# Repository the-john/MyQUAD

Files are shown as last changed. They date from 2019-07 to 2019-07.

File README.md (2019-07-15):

# MyQUAD
First Open Source Arduino Based Quad Copter

Back in the day, gaining access to a Quad Copter wasn't easy.  Especially one that you could intimately know and modify.  I set out to change that.

I wanted to develop a platform that "students" could come to know and understand.  My hope was to inspire students from all walks of life to learn and grow.  I hope I did that with the material in this repository.  After I developed this material, I handed it over to others who promised to make it all publically available.  I'm not convenced that they did a very good job of that.  So, I've placed the materials here in this repository for public consumption.  (Albeit, SEVEN YEARS LATER!)

At the time, I chose to develop the Quad Copter on an Arduino board.  I had already gotten many people, mostly students, excited about the Arduino board with Introductory Training materials that I had created on my own previously.  I knew that the Arduino platform would be easy for NOOBs to wrap thier brain around and get them hooked.  So I designed a Quad Copter Shield and set off to develop a complete kit.  I purposely designed the Shield in Eagle to enable others to modify or embellish via a free tool.

I looked around for a long time to try and find some code that would work on my new platform.  Though there were code options to be had, most of them required a PhD in Computer Programming to debug if you changed the slightest thing.  I knew this would be a buz kill for my following ... so I personally wrote all of the code from scratch in the Programming language.  This code is also included in the attached material, and I hope you find use in opening it up and playing around with it.

The course is meant to be a week long course; four days of lecture and building, one final day for debugging, code upgrading, and a fly-off contest.  So in a week you should be able to go from total NOOB to a flying platform, over 1500 other students have done so themselves.

Good luck, and have some fun with this!

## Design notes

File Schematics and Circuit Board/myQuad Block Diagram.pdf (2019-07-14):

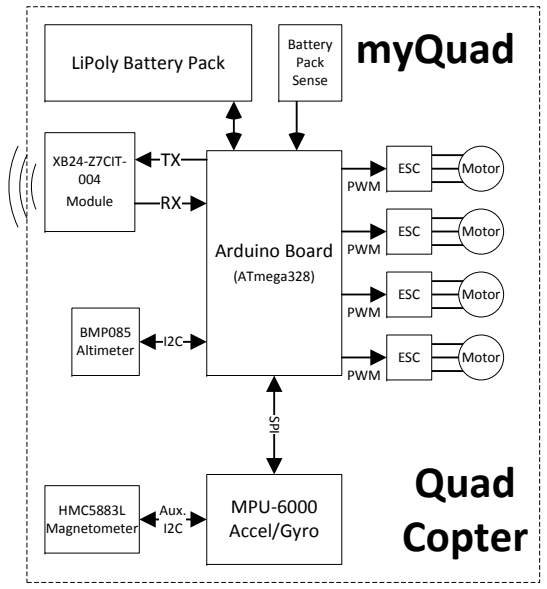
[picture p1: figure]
XB24-Z7CIT- 004 Module; Arduino Board; (ATmega328); Quad Copter; ESC; Motor; PWM; MPU-6000 Accel/Gyro; SPI; LiPoly Battery Pack; Battery Pack Sense; Aux. I2C; BMP085 Altimeter; HMC5883L Magnetometer; myQuad

# Laptop Computer

USB Dongle

## ZigBee Wireless

XB24-Z7CIT-004
Module

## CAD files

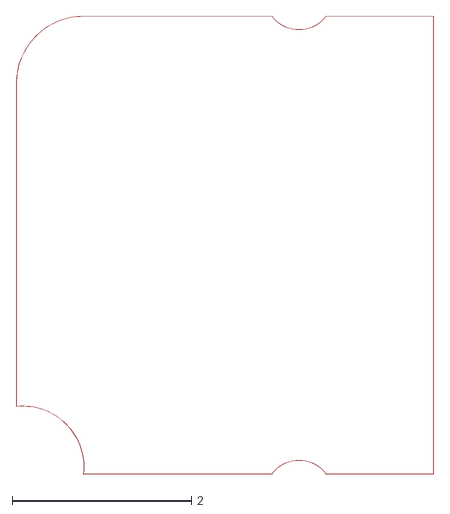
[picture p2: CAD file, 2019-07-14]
Schematics and Circuit Board/Shield Design/Examples/outline.dxf
4.66 x 5.11

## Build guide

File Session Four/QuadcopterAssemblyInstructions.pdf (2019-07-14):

Intel Ultimate Engineering Experience (IUEE)

Chandler Embedded Innovation Center (CEIC)

## IUEE

Quadcopter Assembly
Quadcopter Assembly – IUEE arms and rotors.
You will need the four plastic cutouts for the “landing gear”. One is blue and is the “front” rotor arm. The other 3 are clear plastic. For each rotor, use 2 shiny metal screws from package #1 (8 total), a gold rotor, a blue arm and a plastic landing gear cutout. Repeat for each rotor/arm assembly.
Place the gold rotor on top of a blue arm. Using a Phillips screwdriver, connect the plastic landing gear cutout below the arm with the 2 screws. The screws should connect the plastic landing gear, the arm and the rotor together. The rotor wires should be on the same side (left, when looking toward the center of the copter) of the arm assembly.

[HINT: This might take two team members to hold the components in place.

A shortcut -Try screwing one screw with just the rotor and arm, to align the holes, on the side without the wires. Then screw in the second screw through the plastic landing gear, the arm and the rotor, tightly. Now, remove the first screw (be careful when removing the screw, it may ‘pop’ out at you!), push the plastic landing gear in place and tighten. ] You should now have 4 rotor arm assemblies ready for the next step.
Quadcopter Assembly – rotor arm to center base.
You will need the four rotor arm assemblies, the “odd” shaped center plastic base, 8 black plastic screws, and 8 dull metal standoffs (size?).

Connect each of the 4 rotor arm assemblies to the base using 2 of the screws and the standoffs (as shown in the model).

[HINT: Notice the base pattern. The narrower edges connect to the front and back rotor arm assemblies. The wider edges connect to the side rotor arm assemblies.]
Quadcopter Assembly – rotor arm to center base.
You will need the four rotor arm assemblies, the “odd” shaped center plastic base, 8 black plastic screws, and 8 dull metal standoffs (size?).

Connect each of the 4 rotor arm assemblies to the base using 2 of the screws and the standoffs (as shown in the model).

[HINT: Notice the base pattern. The narrower edges connect to the front and back rotor arm assemblies. The wider edges connect to the side rotor arm assemblies.]
Quadcopter Assembly – Connect Arduino and shield to base.
You will need the center base assembly (assembled with the rotor arms), the Arduino board, the shield board, 4 long plastic standoffs (package #x), 4 short plastic standoffs, 4 long black screws (with a “hex head”), and 4 regular nuts.

The shield will go on top of the Arduino board, separated by the long plastic standoffs. Below that are the short plastic standoffs between the Arduino board and the center base assembly. The four screws go through this whole “stack” of components, and are tightened in place with the regular nuts.

[HINT: This might take two team members to hold the components in place.

Insert a screw thru the shield board, long plastic standoff, and Arduino board. Push the short standoff on, followed by the center base assembly. Tighten loosely, using the nut..

Repeat on an adjacent screw (tilting the board, can be done a bit if the first screw is “loose”). Follow with the next two screws. Then tighten up all 4 screws/nuts.

### Quadcopter Assembly –actuators to rotos

You will need the center base assembly, 4 sets of Velcro, and 4 mini actuator boards.

Connect each set of 3 actuator wires to the rotor. Place the Velcro strip on the bottom of the center base plastic so that the actuator board “lines up” with the green connector on the Shield. Connect up the voltage pins and signal pins. The connectors are + (red wire) and – (black wire) for the voltage pins. The signal pins (green connector) should have the black wire on the board edge and the white wire toward the board center.

[HINT: BE CAREFUL NOT TO JAM THE WIRES TOGETHER TOO HARD. THE WIRES MIGHT BREAK!]

Spin test.
Do a spin test of your rotors. You will need a battery to connect to the Shield board. The front (blue) and rear rotors should be spinning counter-clockwise. The two side rotors should be spinning clockwise.

If a rotor is spinning the wrong direction. Take two of the rotor wires on that rotor and “flip” the connections. This is a 3-phase rotor and that will change the spin direction.

Continue Assembly.
Quadcopter Assembly –Heat shrink placement.
Quadcopter Assembly –center base w/ boards to top plate.
You will need the center base assembly, 8 black nuts, 8 locking nuts, and 8 very long shiny screws (package #).

Connect the top plate (lining up the Intel logo) to the center plate using the nuts and screws.

[HINT: Screw 2 regular nuts down on each screw. Place the screw in the hole on the center assembly. Tighten the locknut. Repeat for other 3 screws. Place the top plate on the screws and tighten the top locknuts. Then tighten the 8 regular nuts, so that the assembly is stable.]

### Quadcopter Assembly – Connect Bottom plate to assembly

You will need the base assembly, 2 velcro straps, 8 black screws, battery, and a voltage buzzer alarm.

Connect the top plate (lining up the Intel logo) to the center plate using the nuts and screws.

[HINT: Screw 2 regular nuts down on each screw. Place the screw in the hole on the center assembly. Tighten the locknut. Repeat for other 3 screws. Place the top plate on the screws and tighten the top locknuts. Then tighten the 8 regular nuts, so that the assembly is stable.]

Position Capacitor Jumpers To Fly

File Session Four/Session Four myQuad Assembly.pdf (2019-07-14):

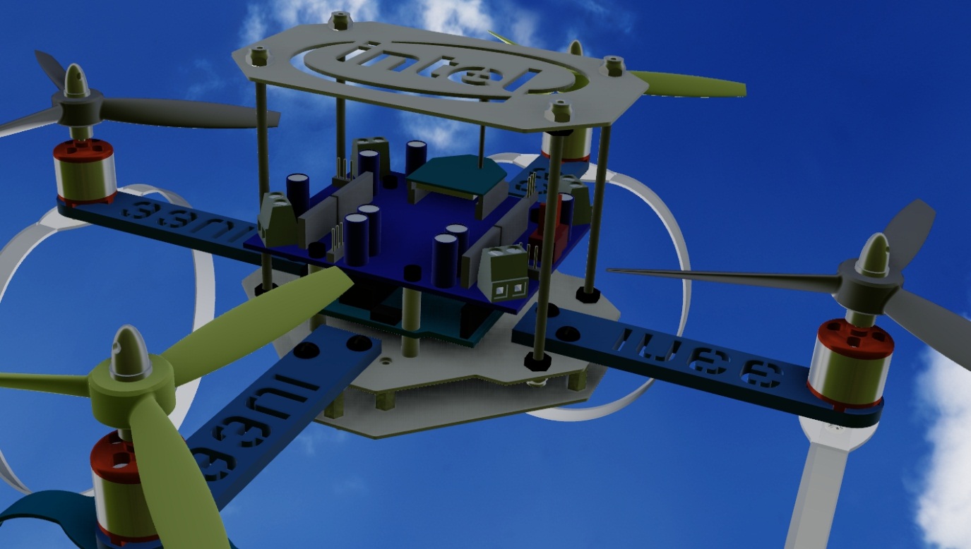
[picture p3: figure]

# Session Four

# Assembly

# Joy Shetler, PhD

# Robotics Week Instructor

# Intel Ultimate Engineering Experience (IUEE)

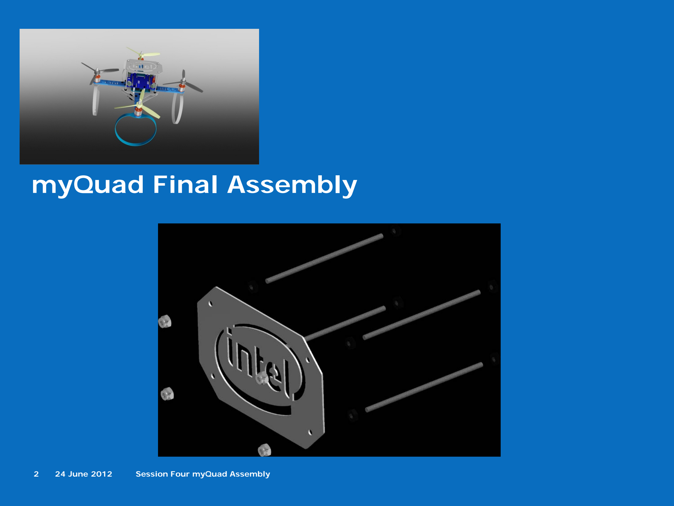
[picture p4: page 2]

2 | 24 June 2012 | Session Four myQuad Assembly

# myQuad Final Assembly

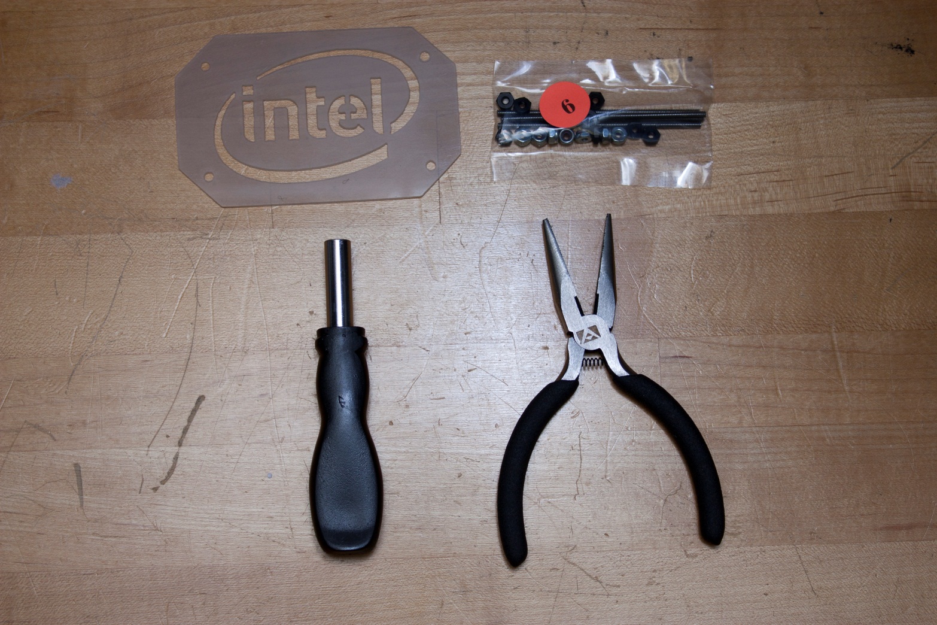
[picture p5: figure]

Chandler Embedded Innovation Center (CEIC)

# Locate Remaining Parts for Crash Protection Plate Mounting

3 24 June, 2012 Session Four myQuad Assembly

# Attach Crash Protection Plate to Mounting Studs

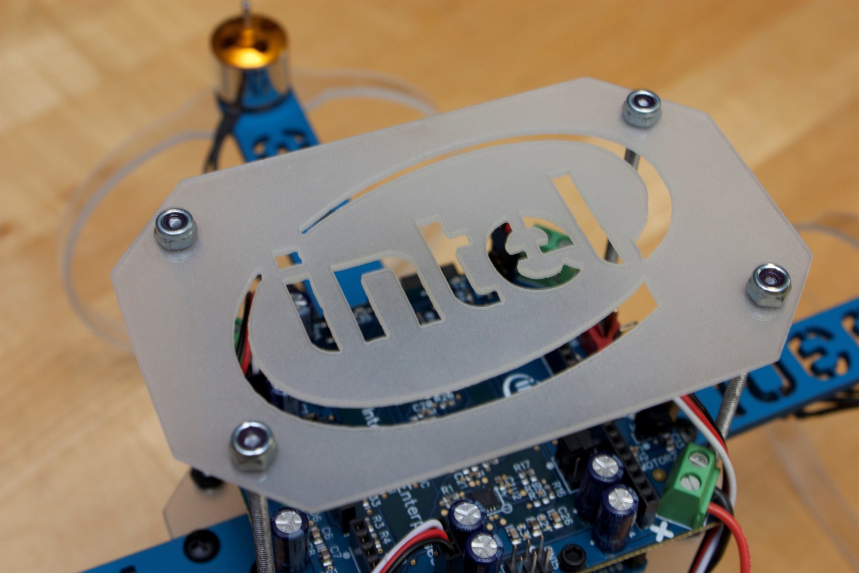
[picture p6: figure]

4 24 June, 2012 Session Four myQuad Assembly

# DANGER

# Do not install propellers until all preliminary testing is

complete.

# Do not run myQuad with propellers outside of

designated safety zone.

5 24 June, 2012 Session Four myQuad Assembly

# Locate Propellers and Propeller Hubs

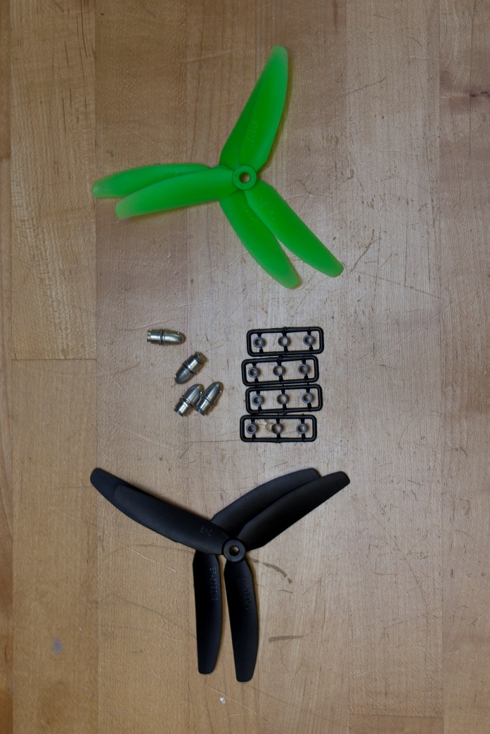
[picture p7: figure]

6 24 June, 2012 Session Four myQuad Assembly

# Attach Propeller Hub Base to Motor Shaft (Insert Plastic Spacer If Applicable)

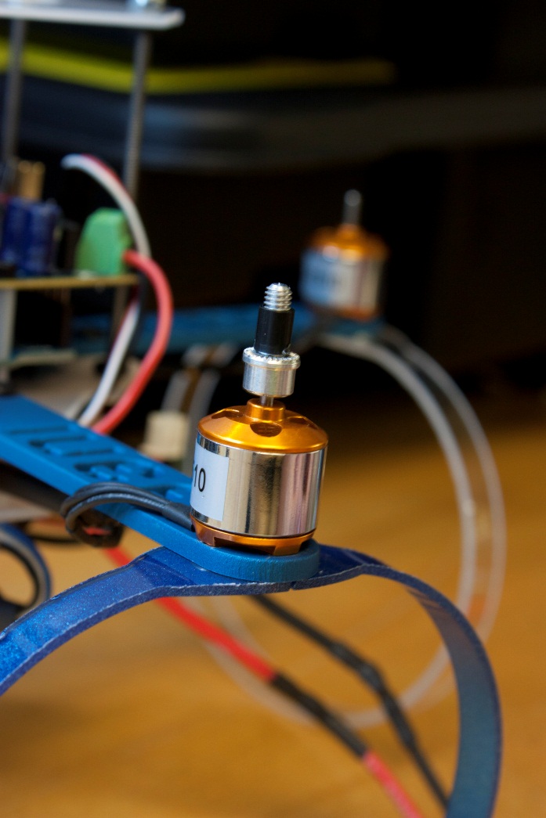
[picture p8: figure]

7 24 June, 2012 Session Four myQuad Assembly

# Slide Propeller Onto Propeller Hub Base

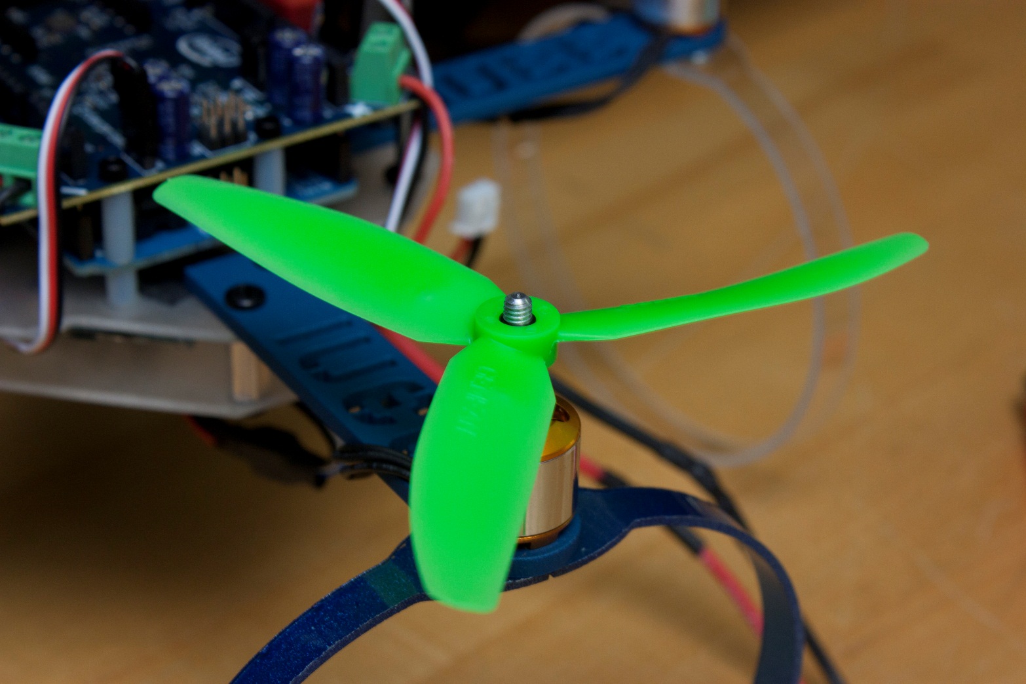
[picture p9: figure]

8 24 June, 2012 Session Four myQuad Assembly

# Attach Propeller Hub Nut, and Tighten

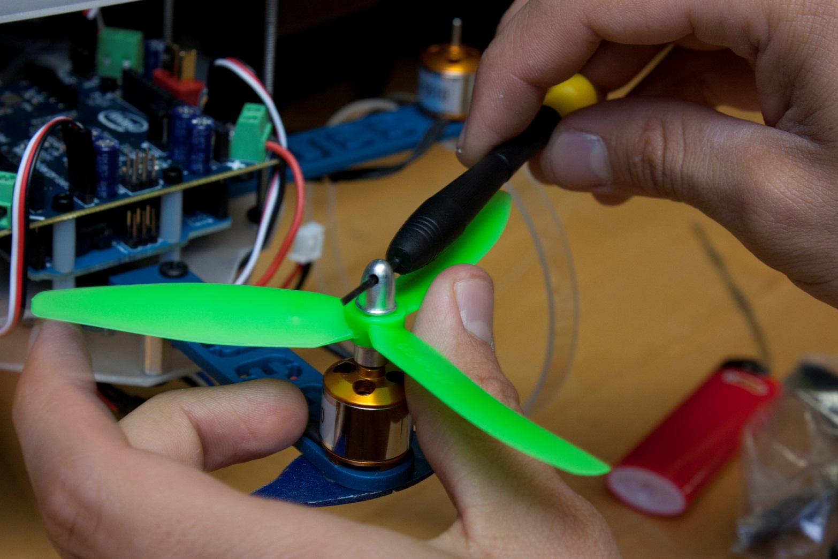
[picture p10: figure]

9 24 June, 2012 Session Four myQuad Assembly

# Front/Back Motors – CW Rotation Props Right/Left Motors – CCW Rotation Props

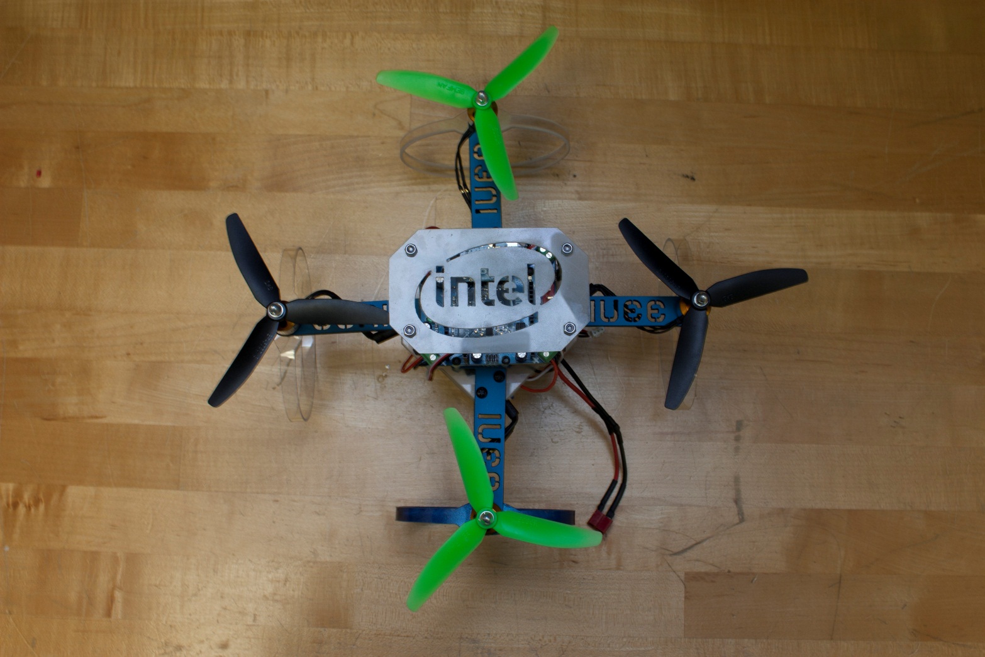
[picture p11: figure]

10 24 June, 2012 Session Four myQuad Assembly

# It’s a beautiful thing…

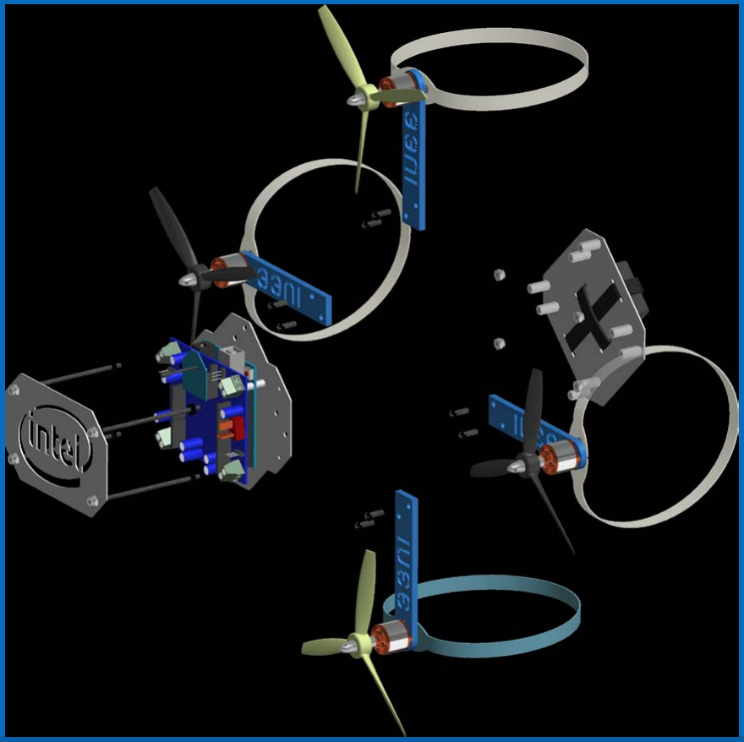
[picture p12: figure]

11 24 June, 2012 Session Four myQuad Assembly

# GO FLY!

12 24 June, 2012 Session Four myQuad Assembly

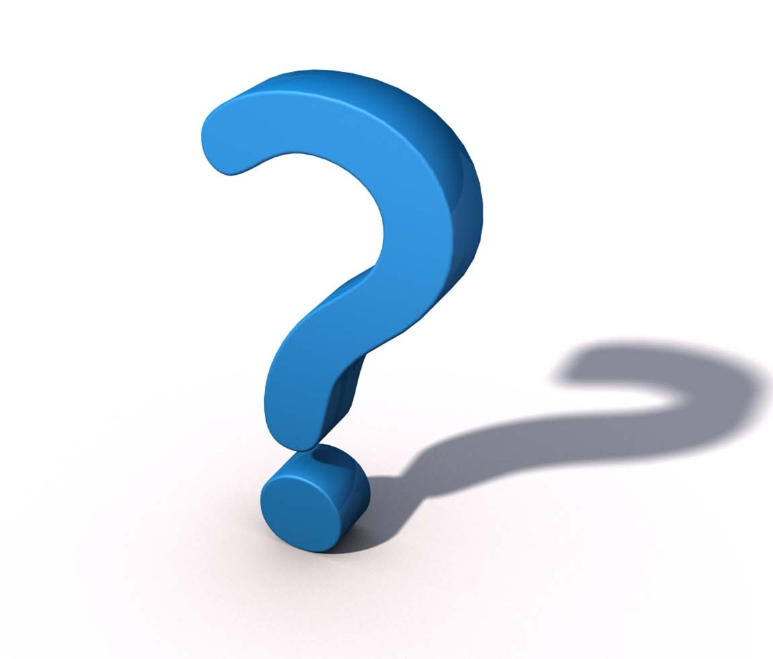
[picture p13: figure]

13 | 24 June, 2012 | Session Four myQuad Assembly

# Questions?

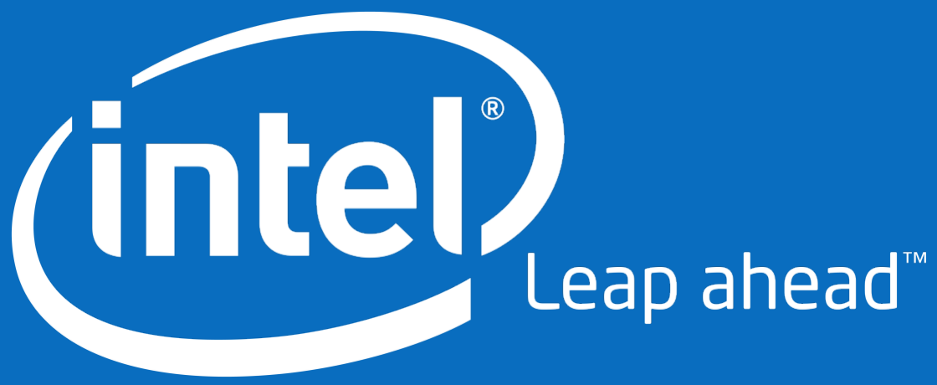
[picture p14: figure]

15 | 24 June, 2012 | Session Four myQuad Assembly

# Backup

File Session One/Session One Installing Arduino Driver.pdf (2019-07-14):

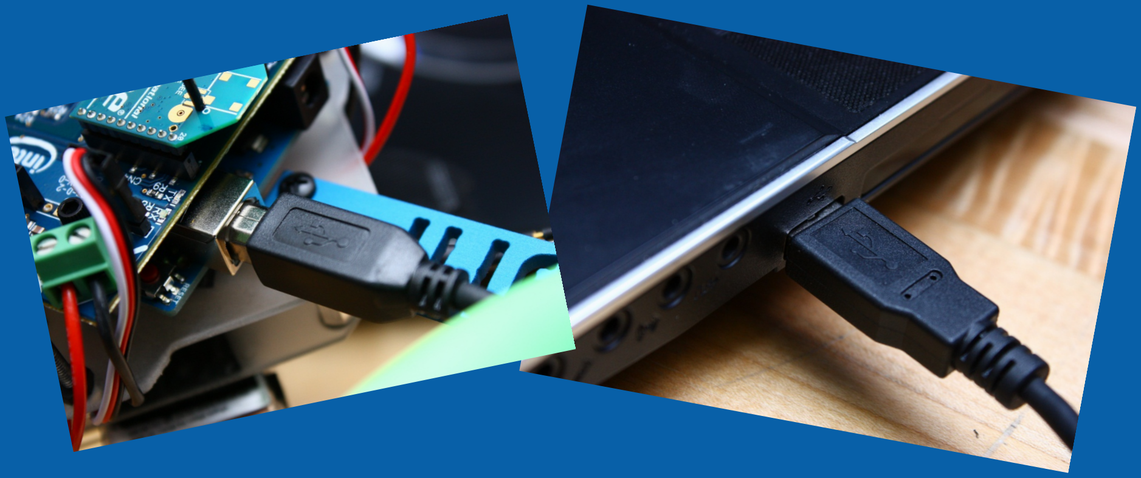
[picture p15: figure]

# Session One

# Installing Arduino Driver

# Joy Shetler, PhD

# Robotics Week Instructor

# Intel Ultimate Engineering Experience (IUEE)

# Connect your Arduino to the Computer

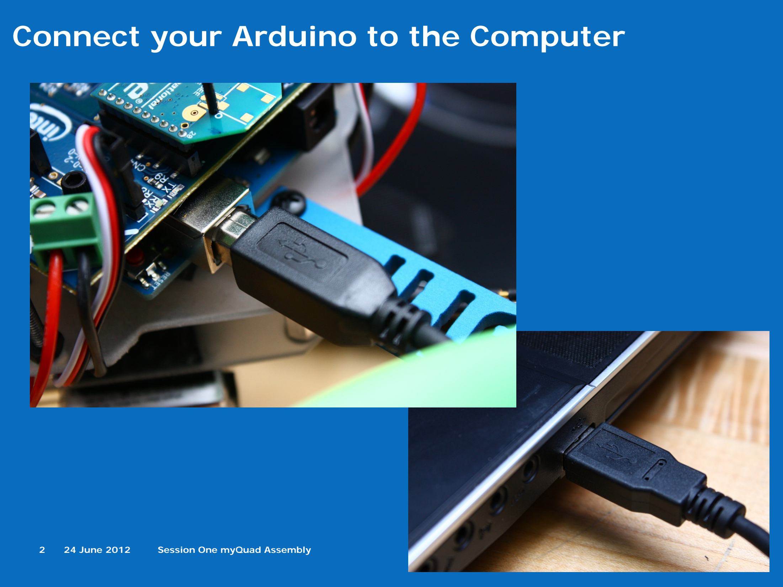
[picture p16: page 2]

2 | 24 June 2012 | Session One myQuad Assembly

# Window Wont Install Drivers

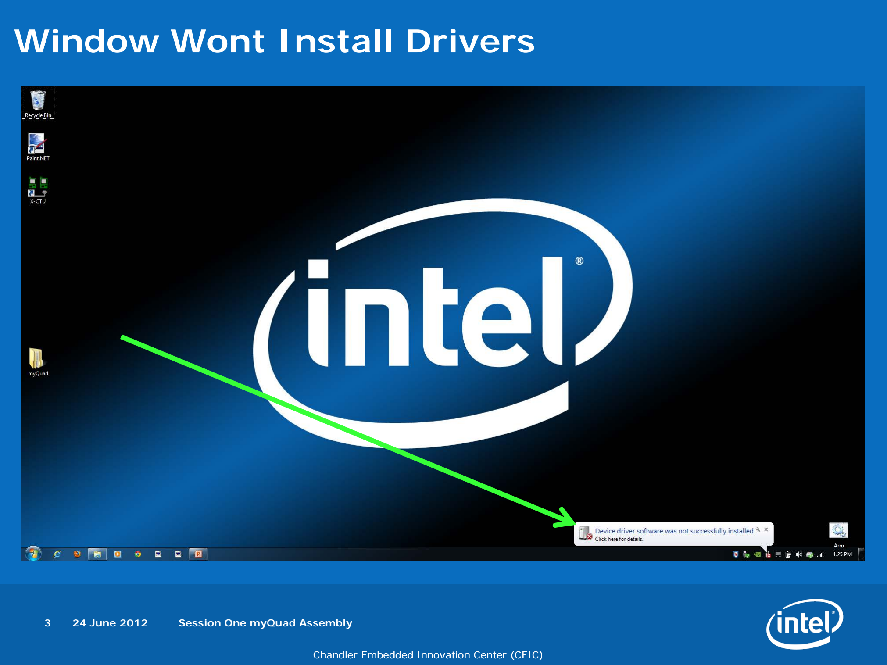
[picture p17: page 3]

Chandler Embedded Innovation Center (CEIC)

3 | 24 June 2012 | Session One myQuad Assembly

# Open Device Manager

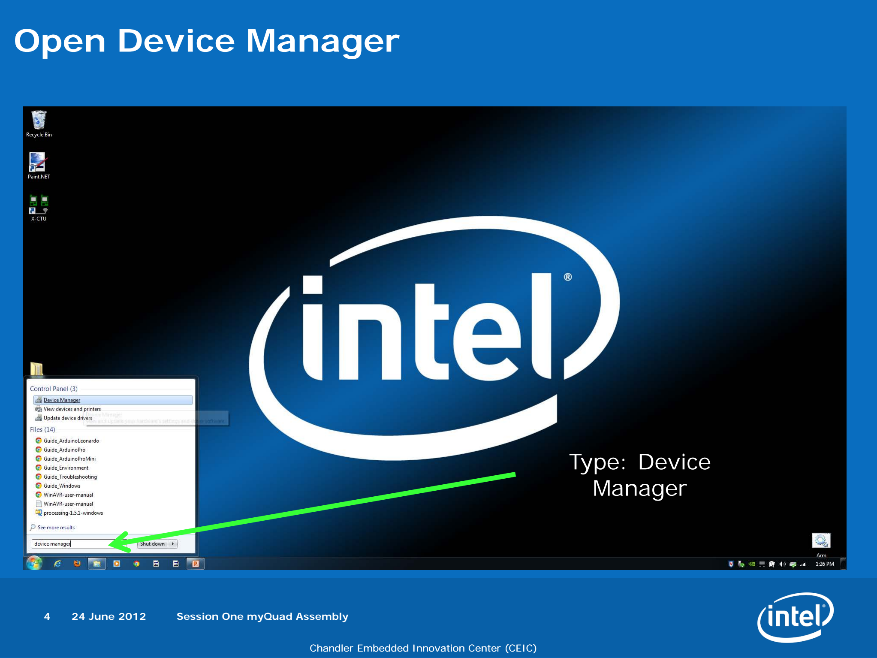
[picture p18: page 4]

4 | 24 June 2012 | Session One myQuad Assembly

# Type: Device Manager

# Right Click – Update Software

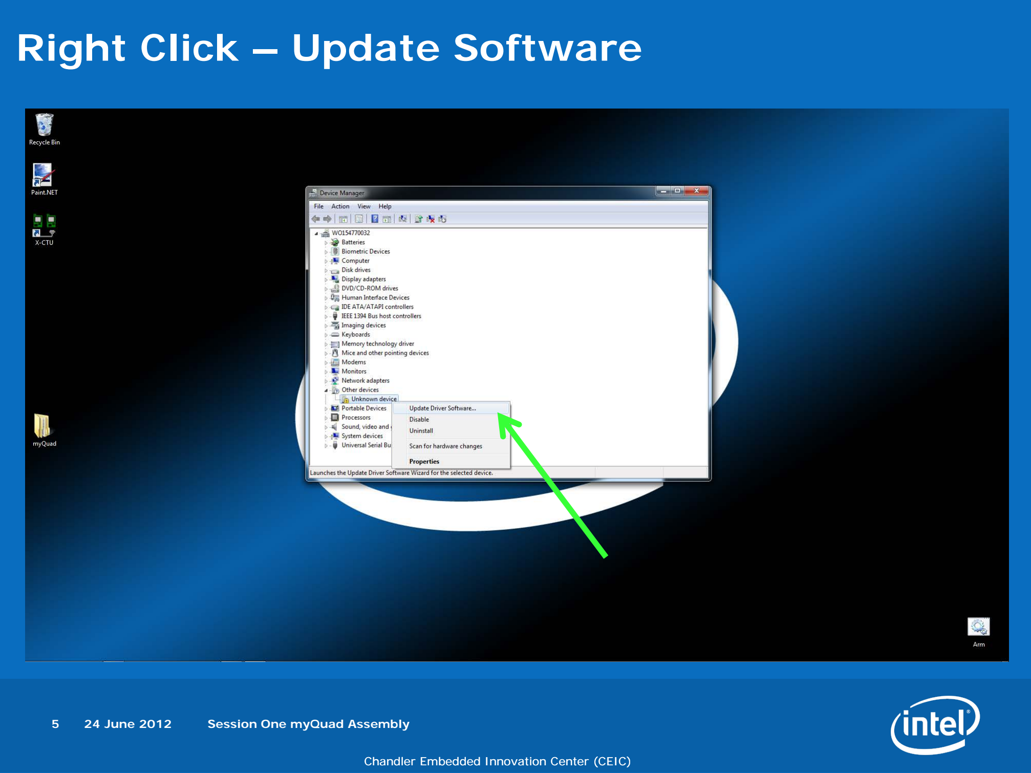
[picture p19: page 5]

5 | 24 June 2012 | Session One myQuad Assembly

# Browse my computer device software

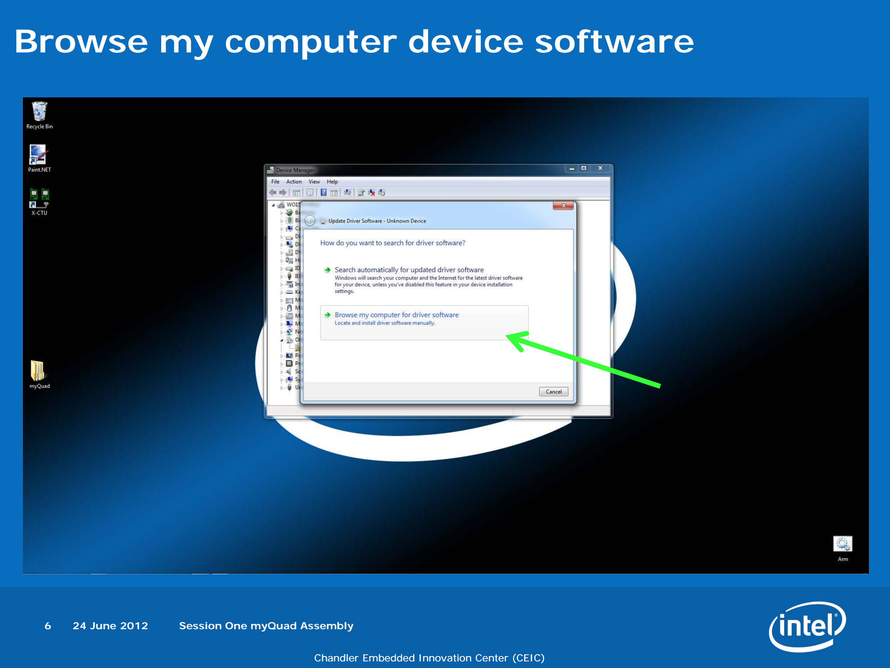
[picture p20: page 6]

6 | 24 June 2012 | Session One myQuad Assembly

# Click Browse

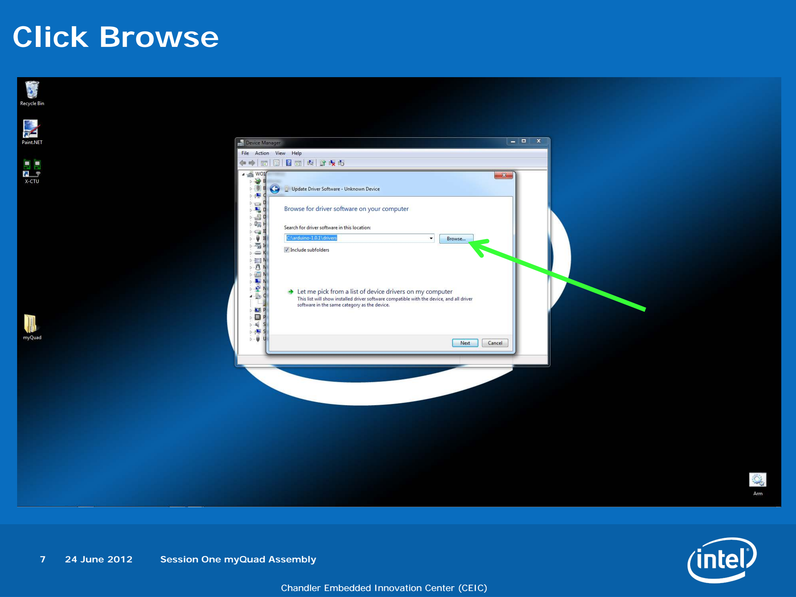
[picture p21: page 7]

7 | 24 June 2012 | Session One myQuad Assembly

# Navigate to:

# C:\Users\Intel\Desktop\myQuad\Downloads\Arduino\arduino-1.0.1\drivers

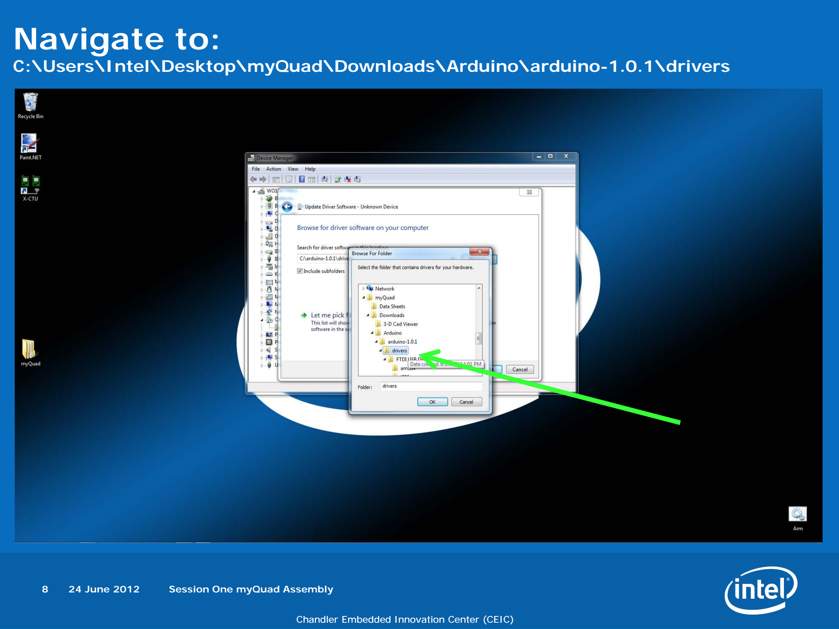
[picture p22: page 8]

8 | 24 June 2012 | Session One myQuad Assembly

# Click OK

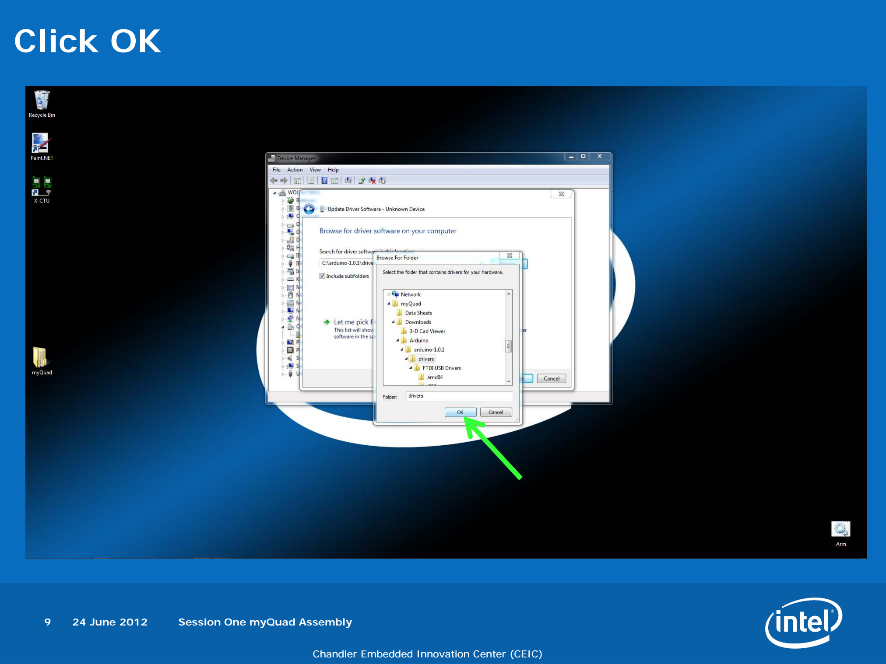
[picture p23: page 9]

9 | 24 June 2012 | Session One myQuad Assembly

# Click Next

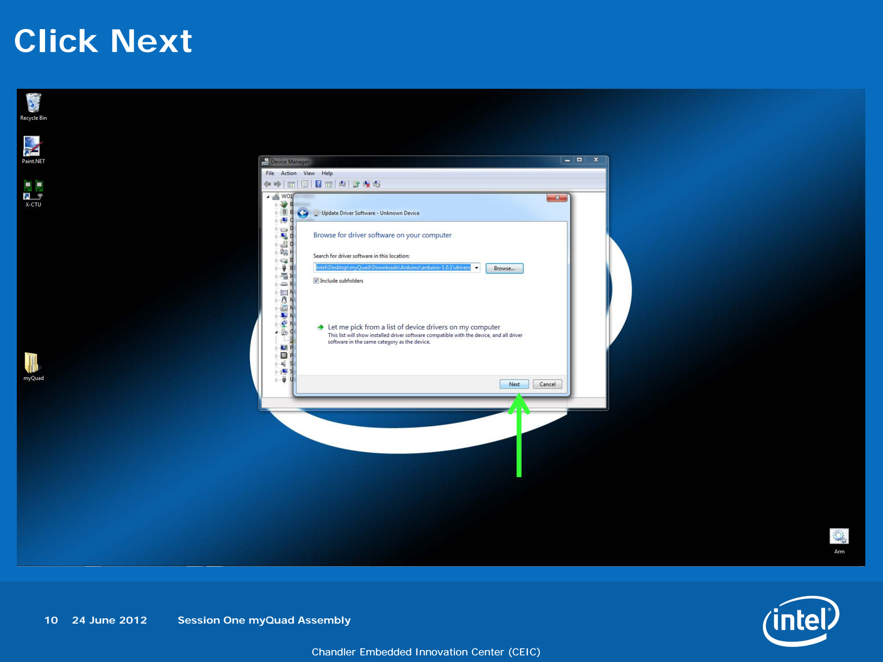
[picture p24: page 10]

10 24 June 2012 Session One myQuad Assembly

# Click Install Anyways

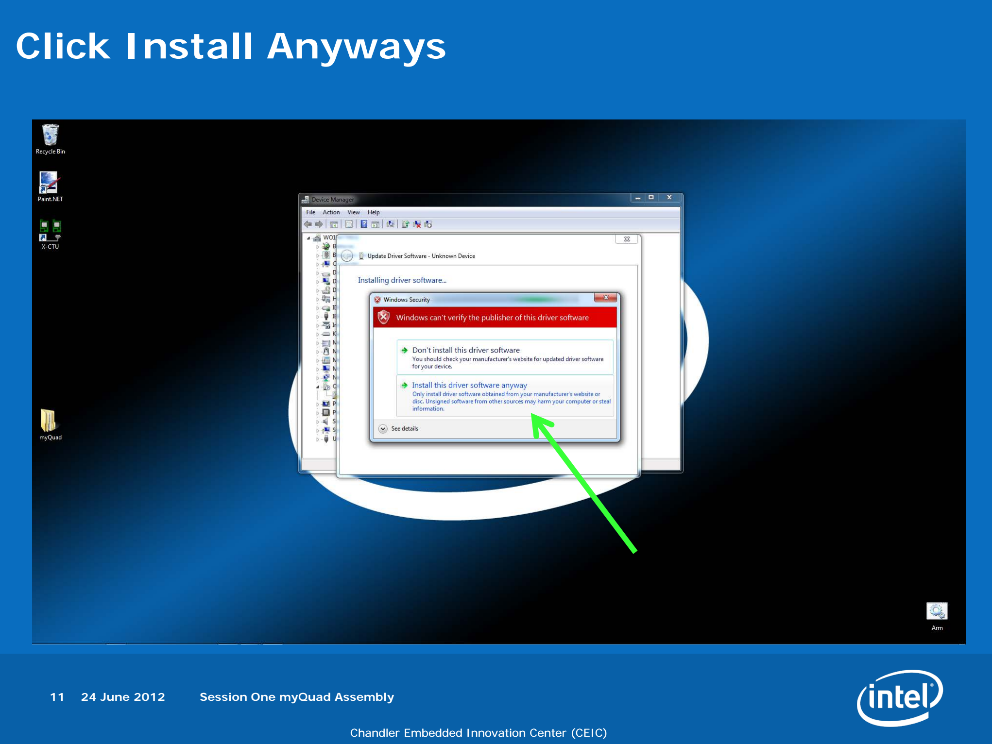
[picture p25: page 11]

11 24 June 2012 Session One myQuad Assembly

# Click Close

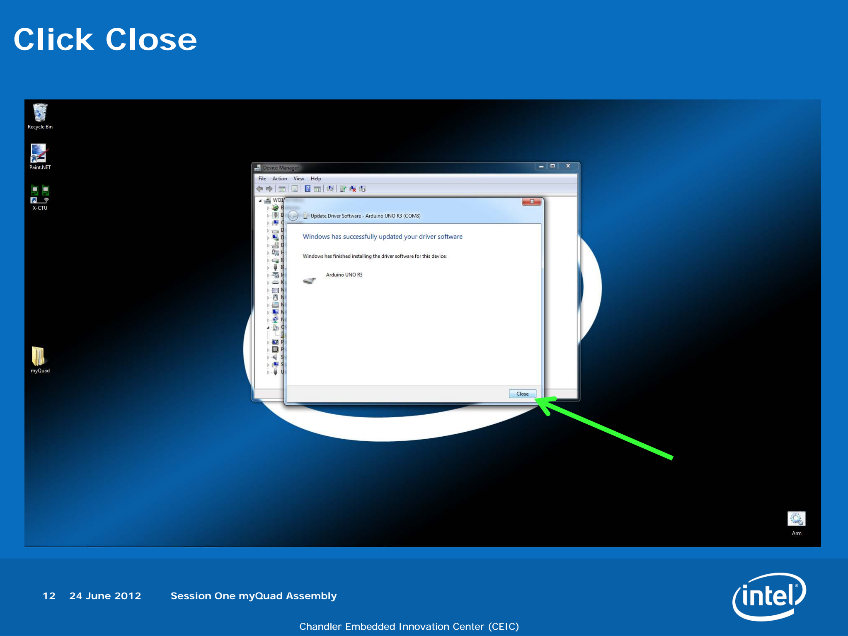
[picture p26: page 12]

12 24 June 2012 Session One myQuad Assembly

# Take note of Port Number

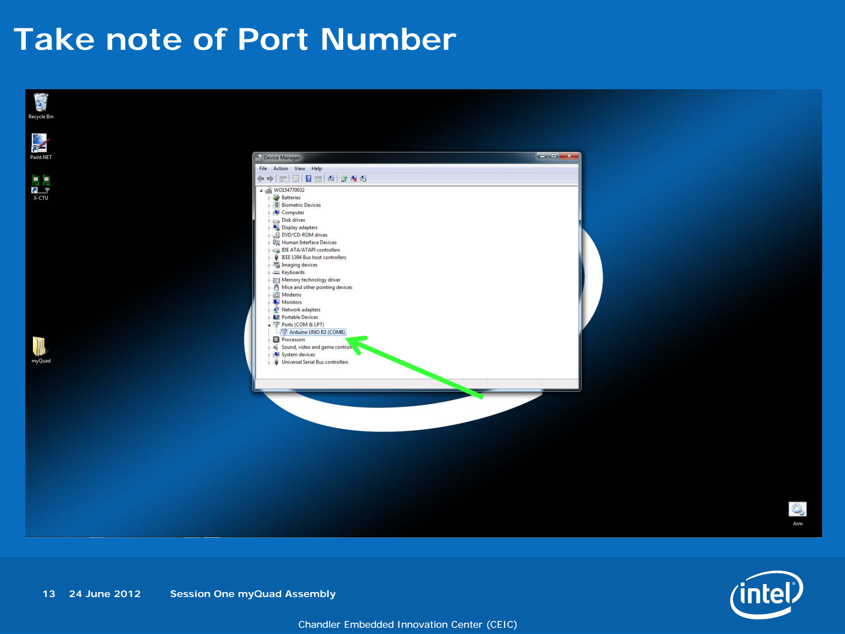
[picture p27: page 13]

13 24 June 2012 Session One myQuad Assembly


15 | 24 June, 2012 | Session One myQuad Assembly

# Backup

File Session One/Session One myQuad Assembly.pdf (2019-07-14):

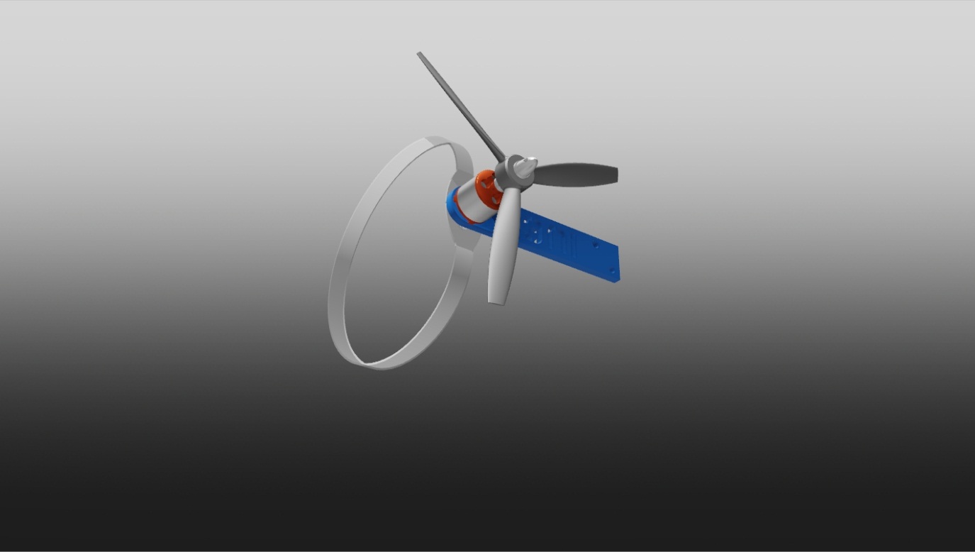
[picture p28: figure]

# Session One

# Assembly

# Joy Shetler, PhD

# Robotics Week Instructor

# Intel Ultimate Engineering Experience (IUEE)

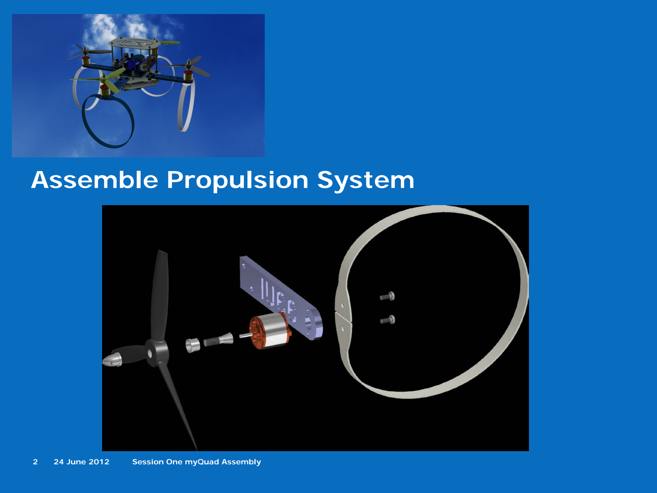
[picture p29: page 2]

2 | 24 June 2012 | Session One myQuad Assembly

# Assemble Propulsion System

# Open myQuad Kit

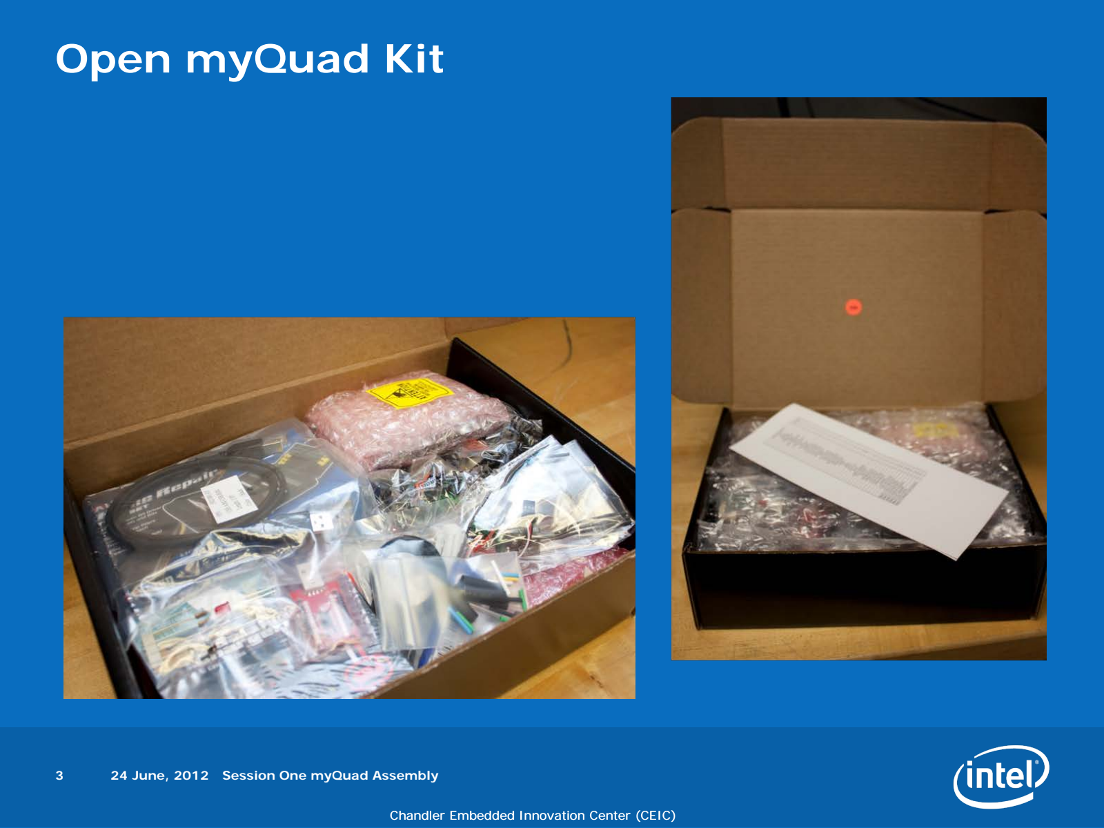
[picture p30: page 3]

Chandler Embedded Innovation Center (CEIC)

3 24 June, 2012 Session One myQuad Assembly

# Everything Necessary for myQuad Build Is Included

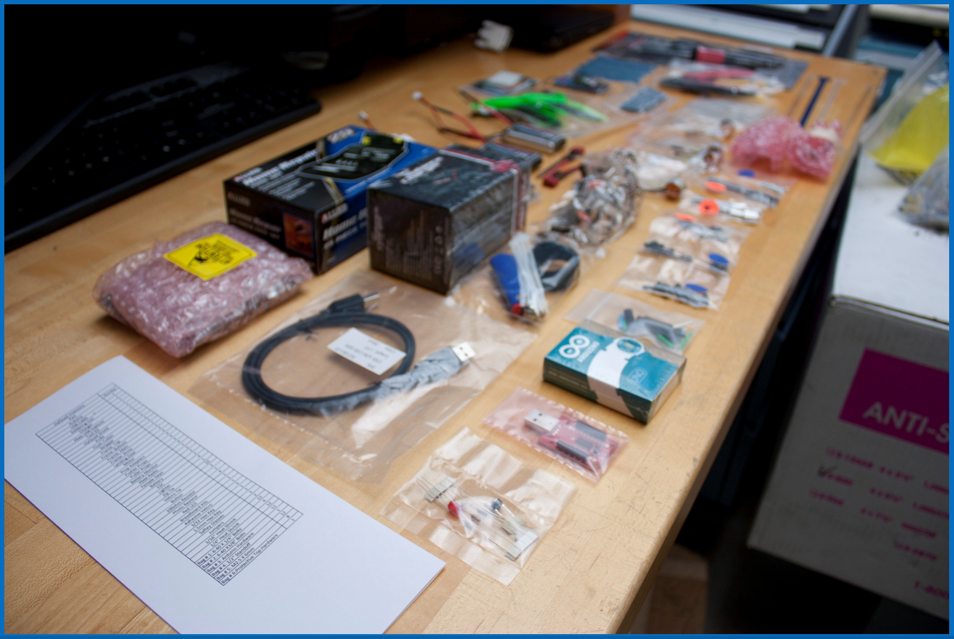
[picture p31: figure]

4 24 June, 2012 Session One myQuad Assembly

# Pull Out Parts For Propulsion System

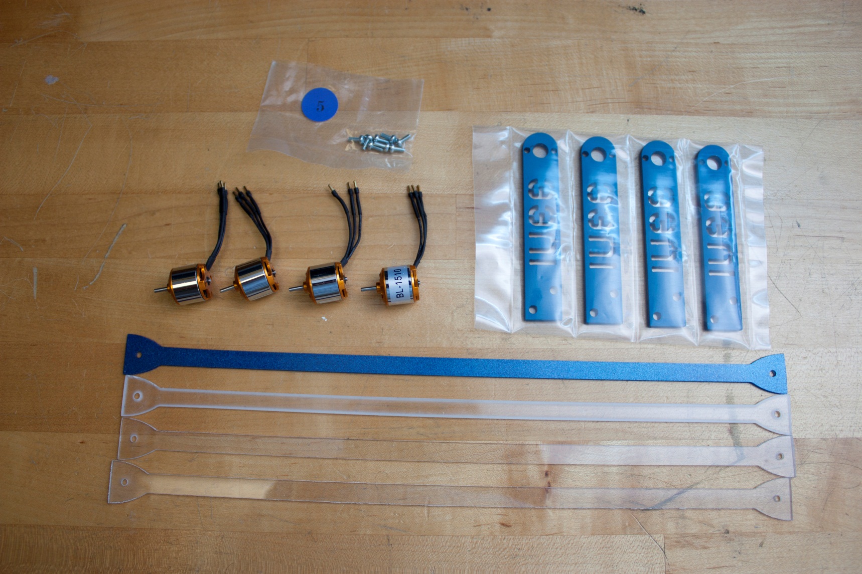
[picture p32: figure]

5 24 June, 2012 Session One myQuad Assembly

# Attach Motor, Arm, And Landing Gear with Two Screws

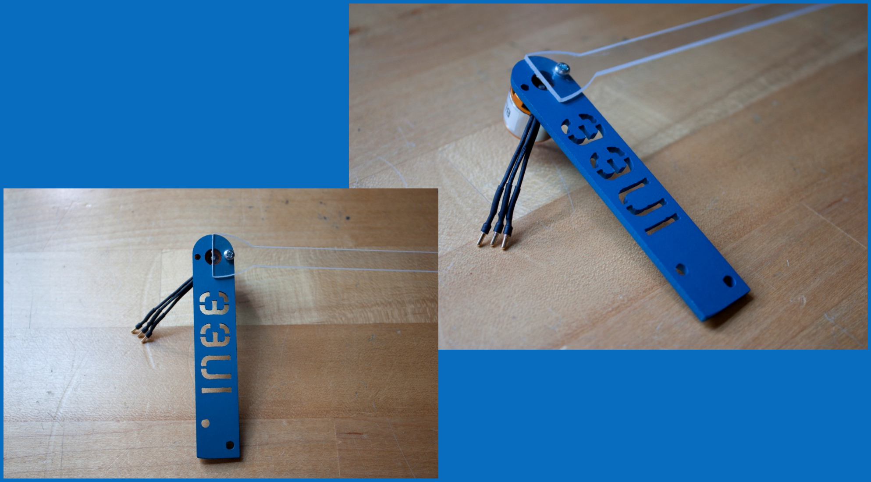
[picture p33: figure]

6 24 June, 2012 Session One myQuad Assembly

# Build All Four Propulsion Assemblies

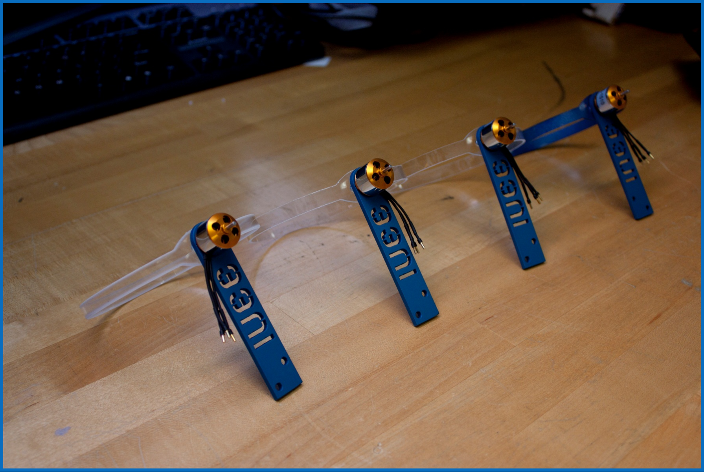
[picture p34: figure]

7 24 June, 2012 Session One myQuad Assembly

# Final Assembly

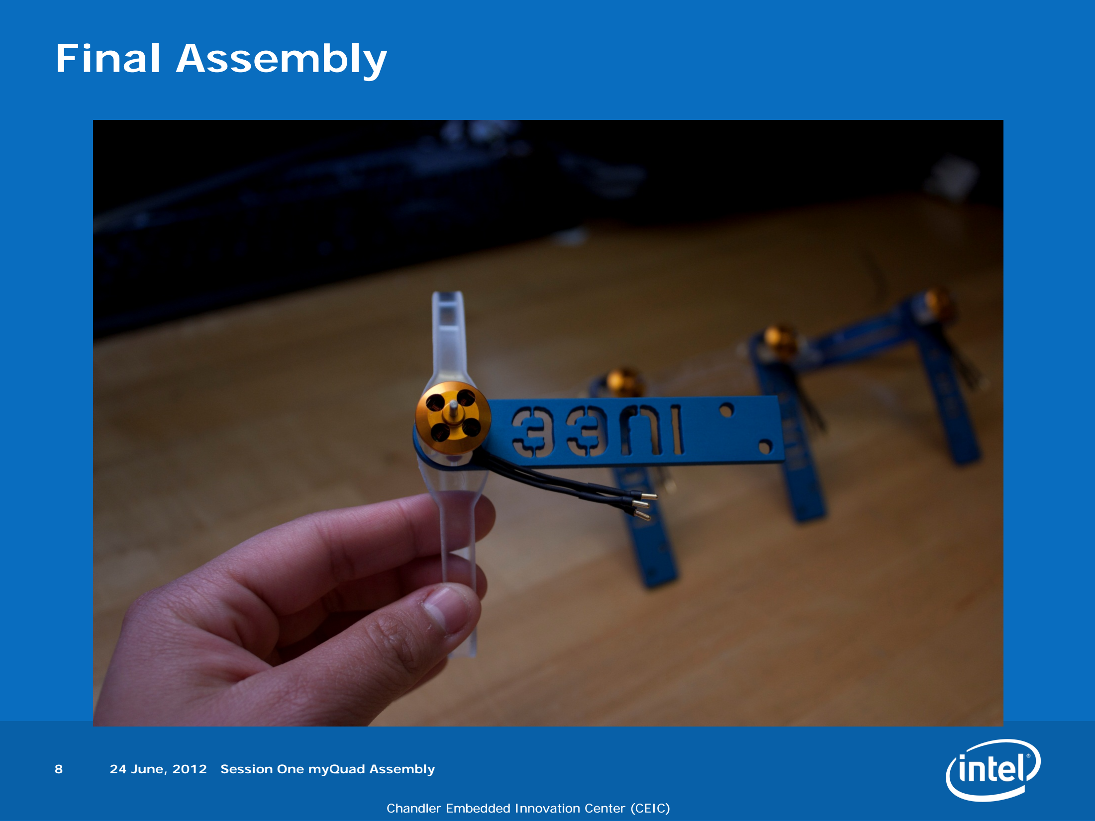
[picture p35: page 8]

8 24 June, 2012 Session One myQuad Assembly

# Start Charging One Battery Pack

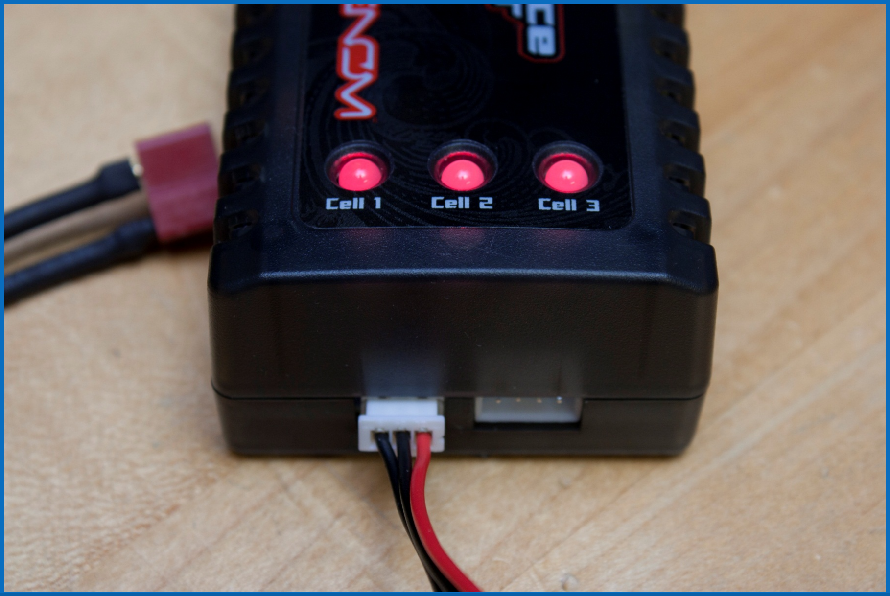
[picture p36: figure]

9 24 June, 2012 Session One myQuad Assembly


10 | 24 June, 2012 | Session One myQuad Assembly

# Questions?


12 | 24 June, 2012 | Session One myQuad Assembly

# Backup

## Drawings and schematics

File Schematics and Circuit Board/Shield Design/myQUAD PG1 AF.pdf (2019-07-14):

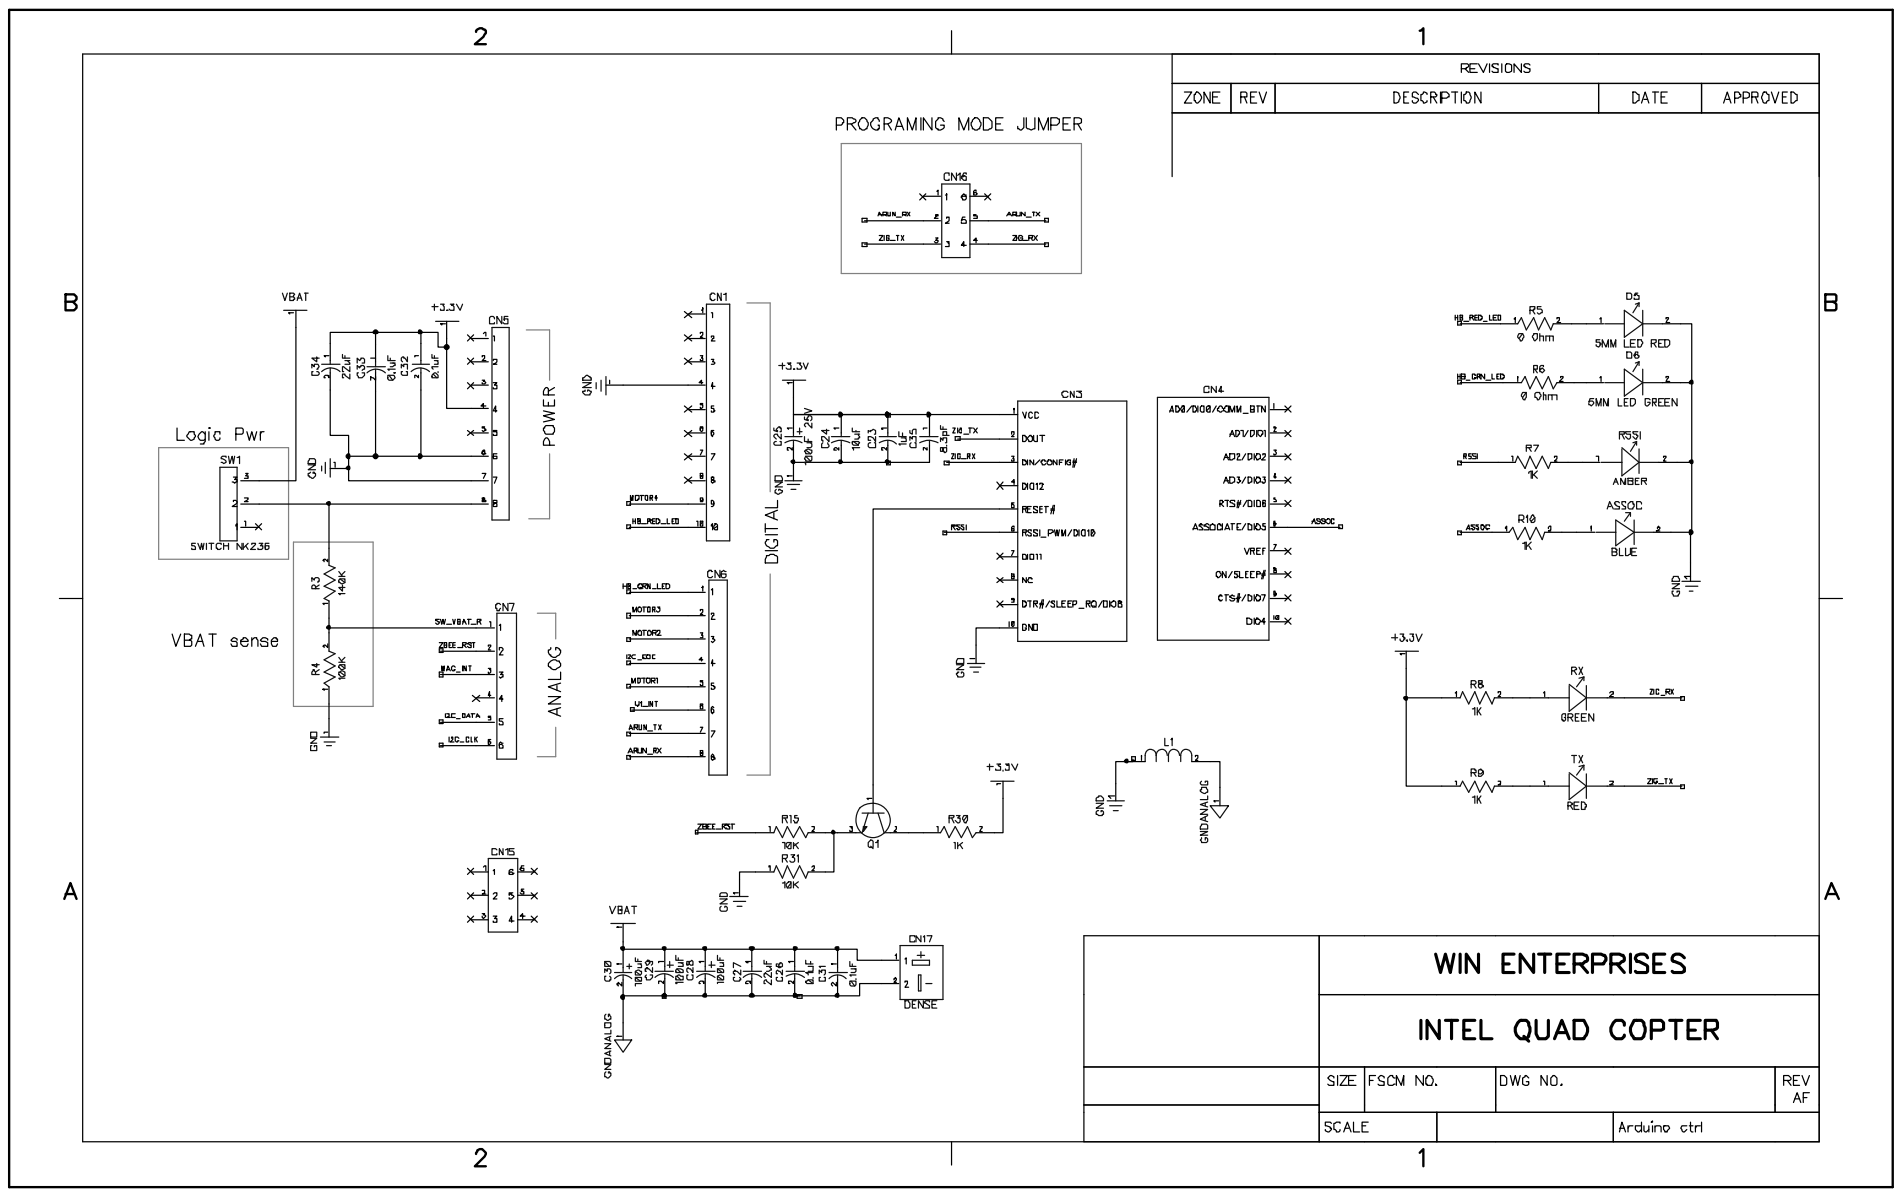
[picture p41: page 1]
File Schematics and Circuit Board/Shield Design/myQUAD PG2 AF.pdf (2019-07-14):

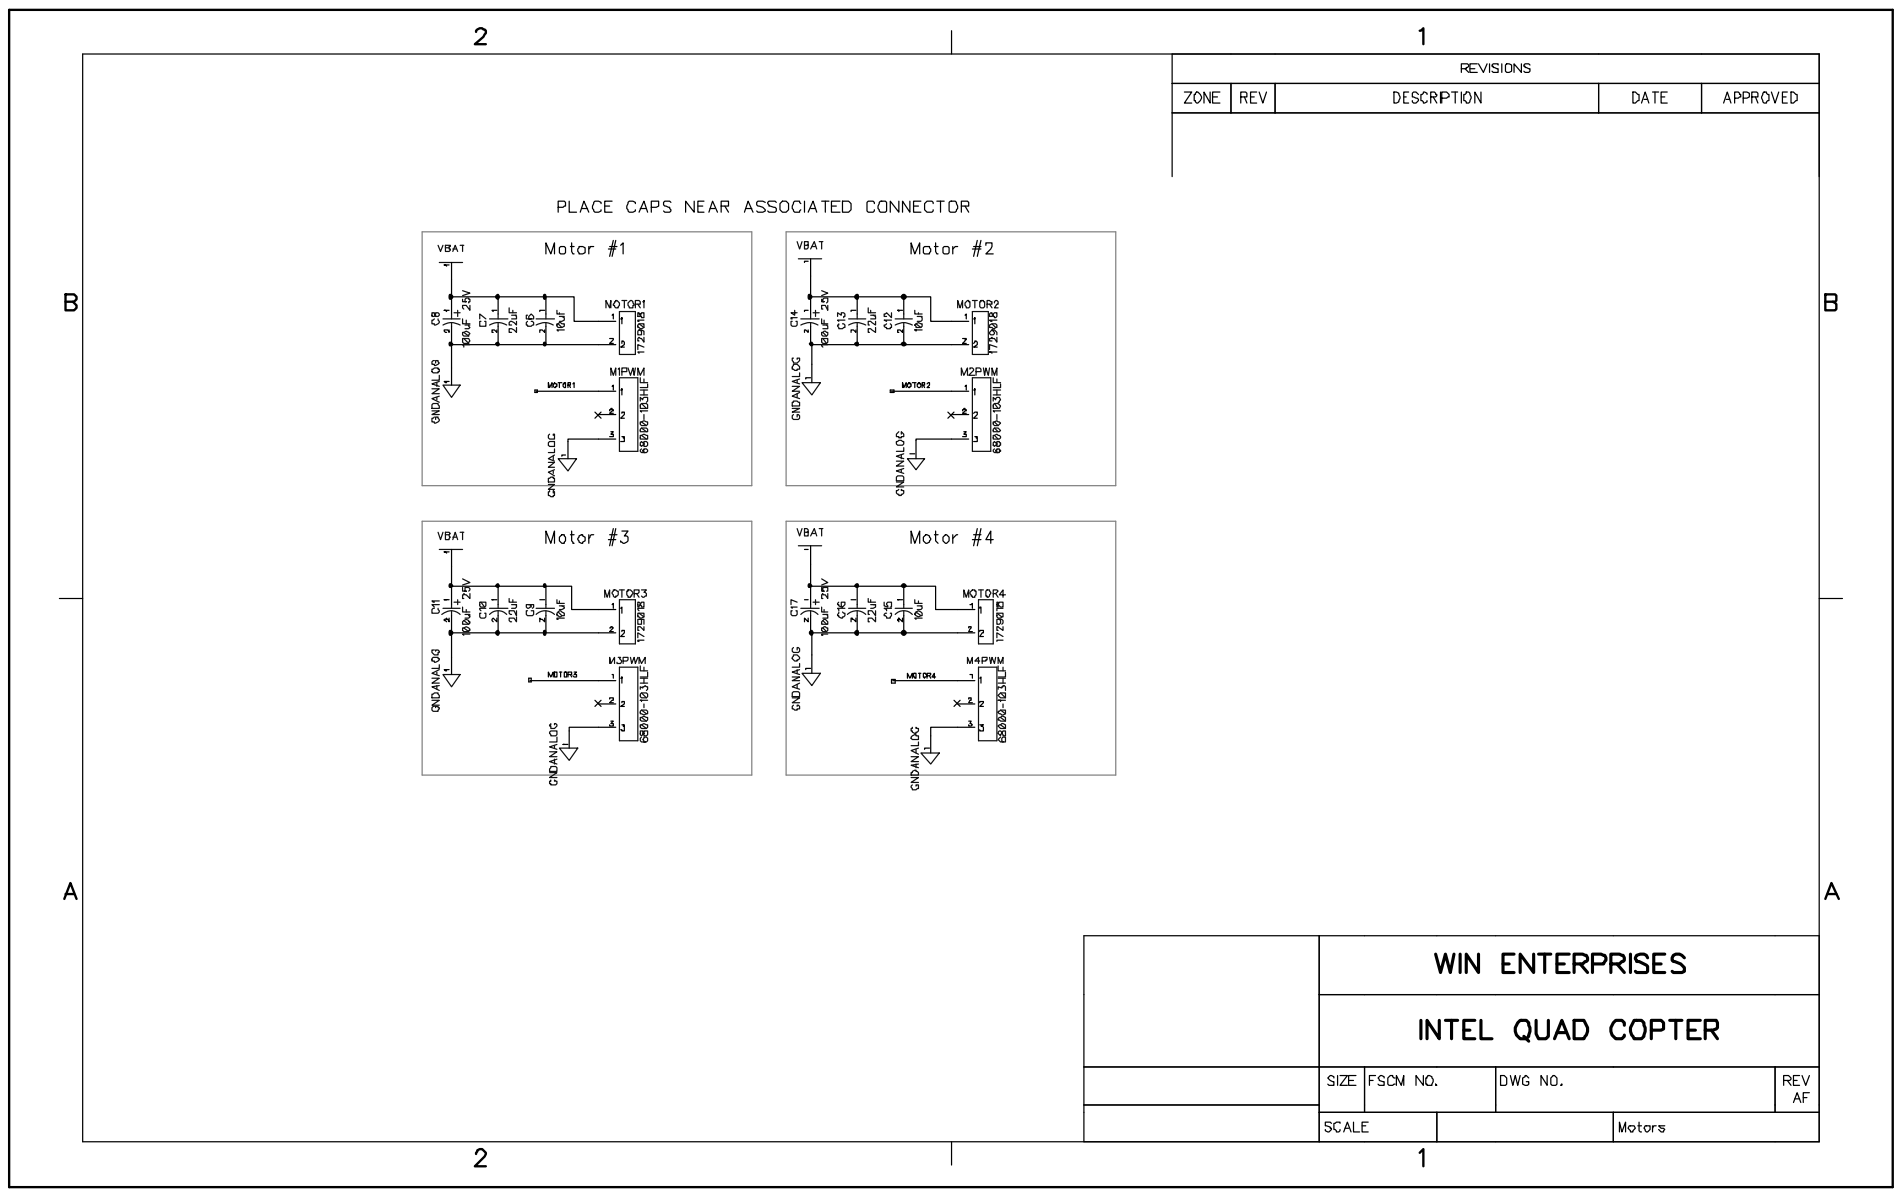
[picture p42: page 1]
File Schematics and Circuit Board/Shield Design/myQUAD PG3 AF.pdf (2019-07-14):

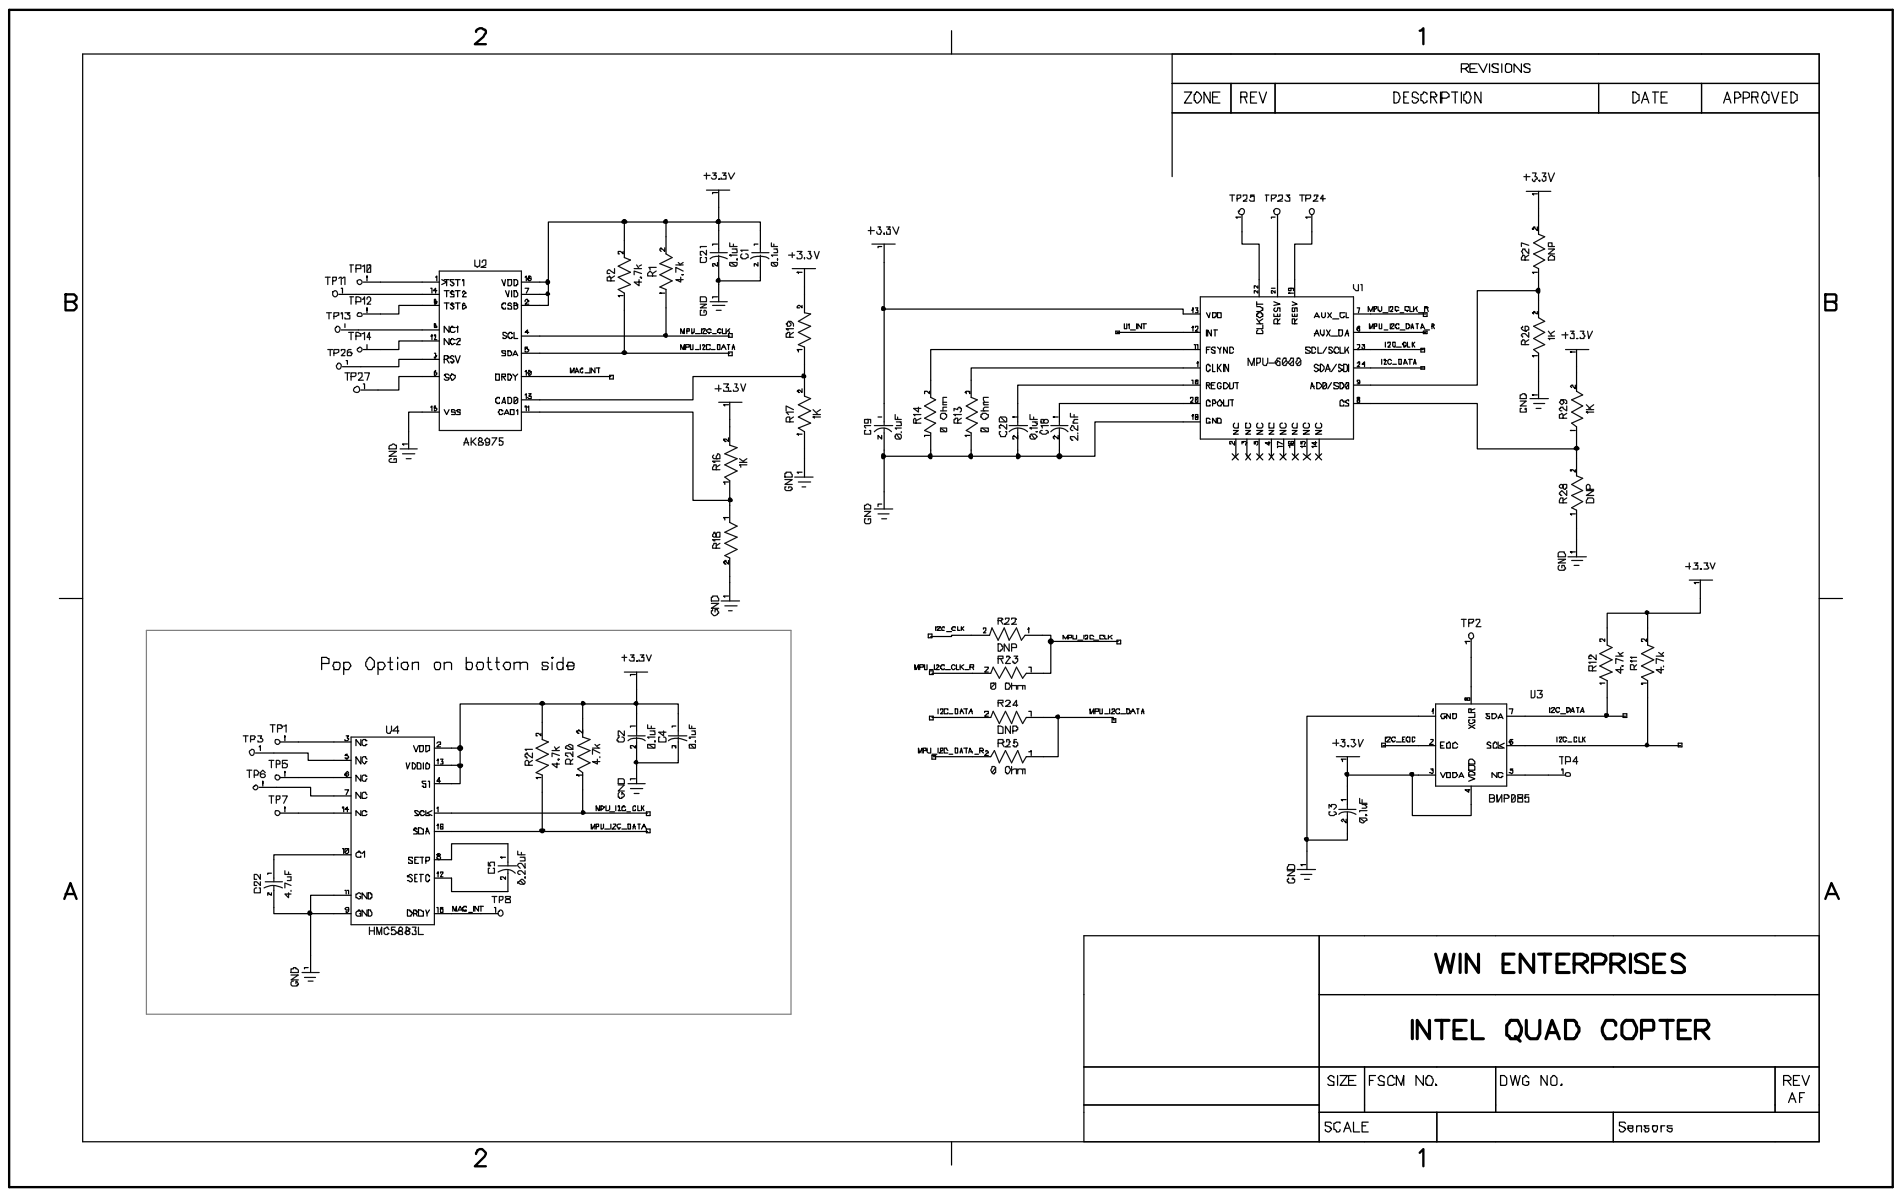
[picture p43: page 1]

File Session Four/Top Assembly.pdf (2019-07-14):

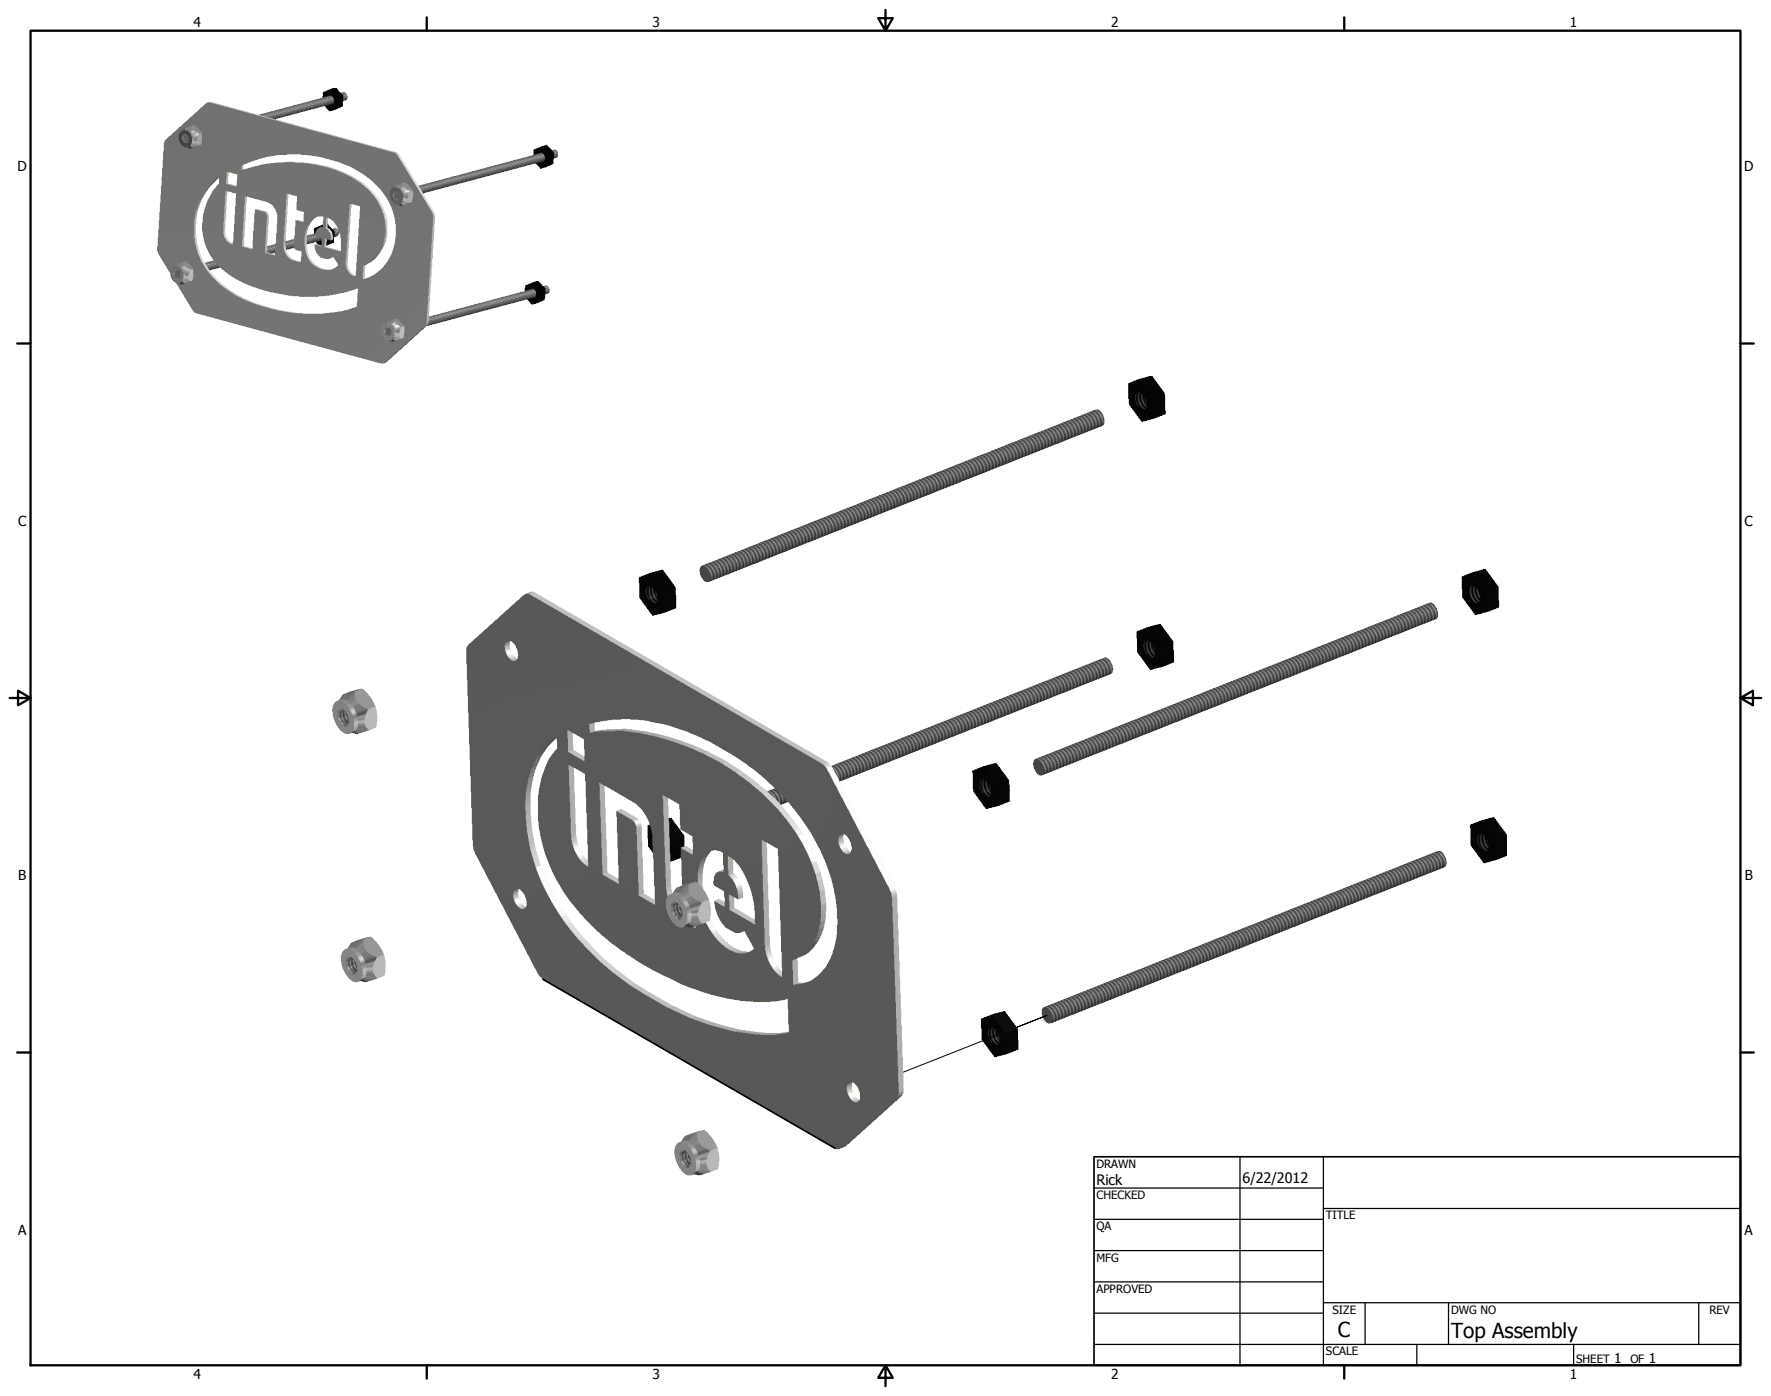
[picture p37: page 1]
SHEET 1 OF 1; DRAWN; CHECKED; MFG; APPROVED; Rick; DWG NO Top Assembly; TITLE; SIZE C; SCALE; REV

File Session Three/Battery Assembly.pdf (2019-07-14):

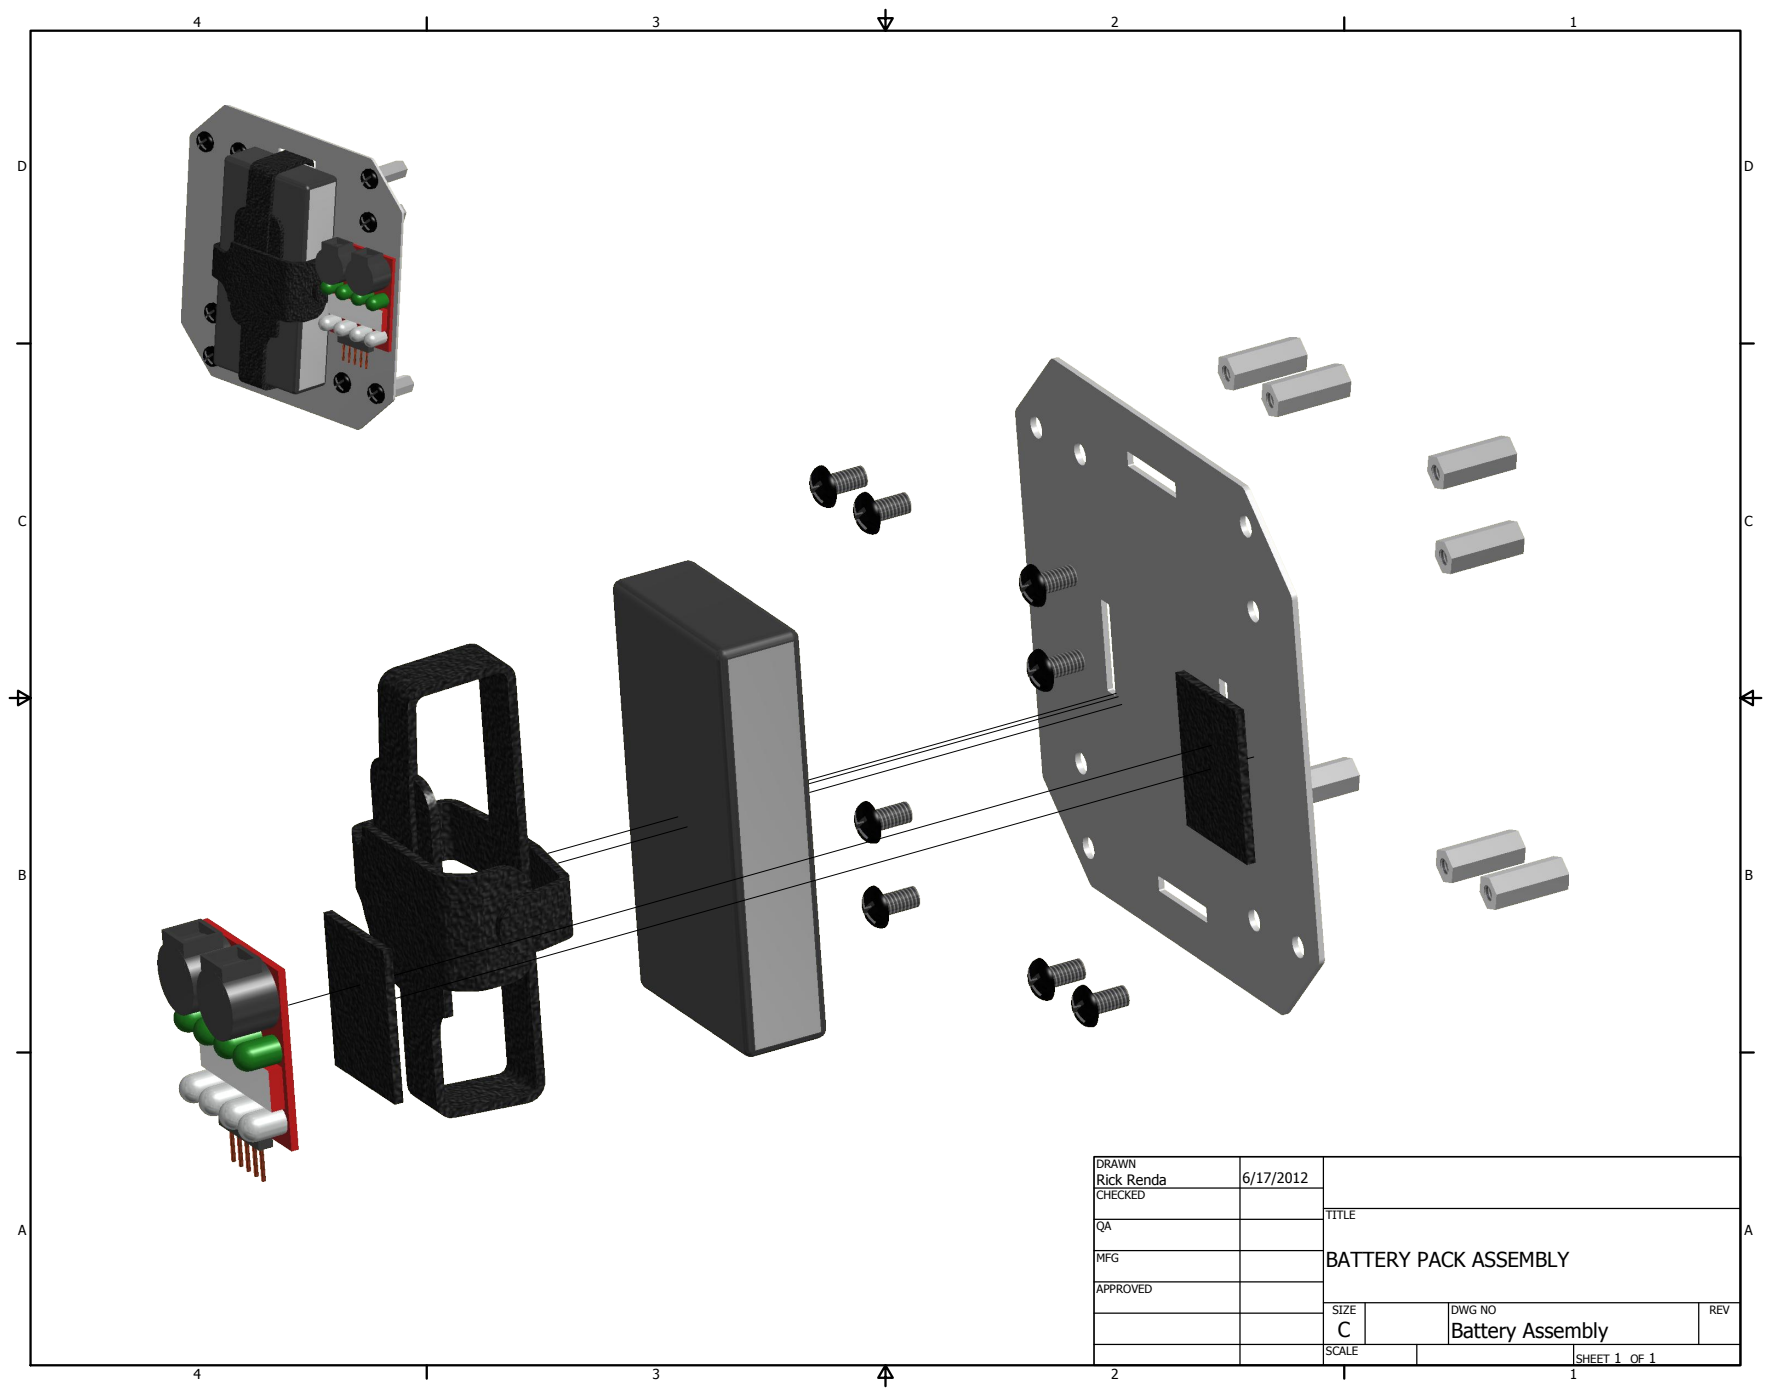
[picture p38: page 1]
SHEET 1 OF 1; DRAWN; CHECKED; MFG; APPROVED; Rick Renda; DWG NO Battery Assembly; TITLE; SIZE C; SCALE; REV

BATTERY PACK ASSEMBLY

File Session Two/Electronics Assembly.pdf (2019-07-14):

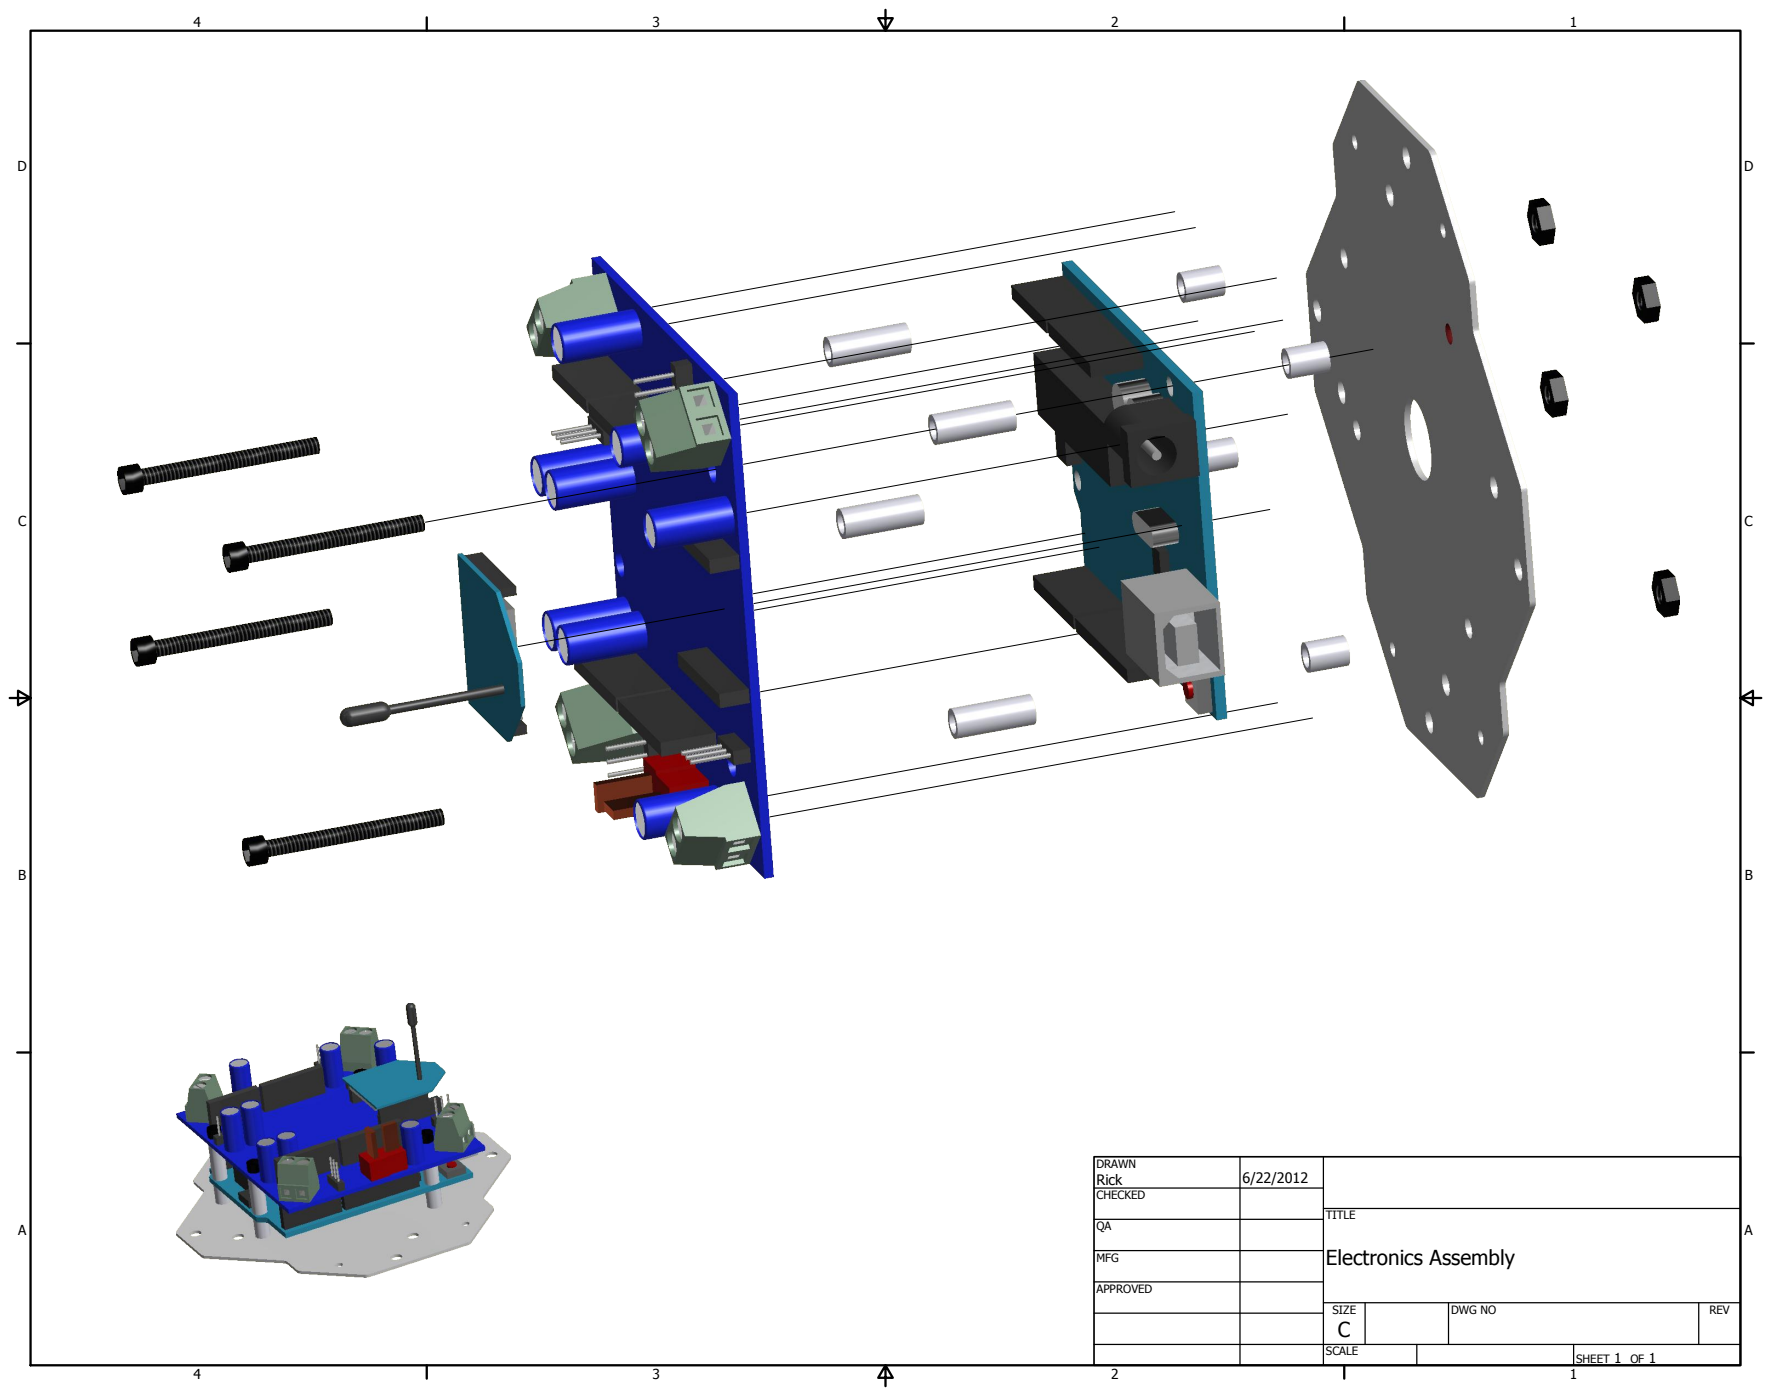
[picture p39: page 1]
SHEET 1 OF 1; DRAWN; CHECKED; MFG; APPROVED; Rick; DWG NO; TITLE; Electronics Assembly; SIZE C; SCALE; REV

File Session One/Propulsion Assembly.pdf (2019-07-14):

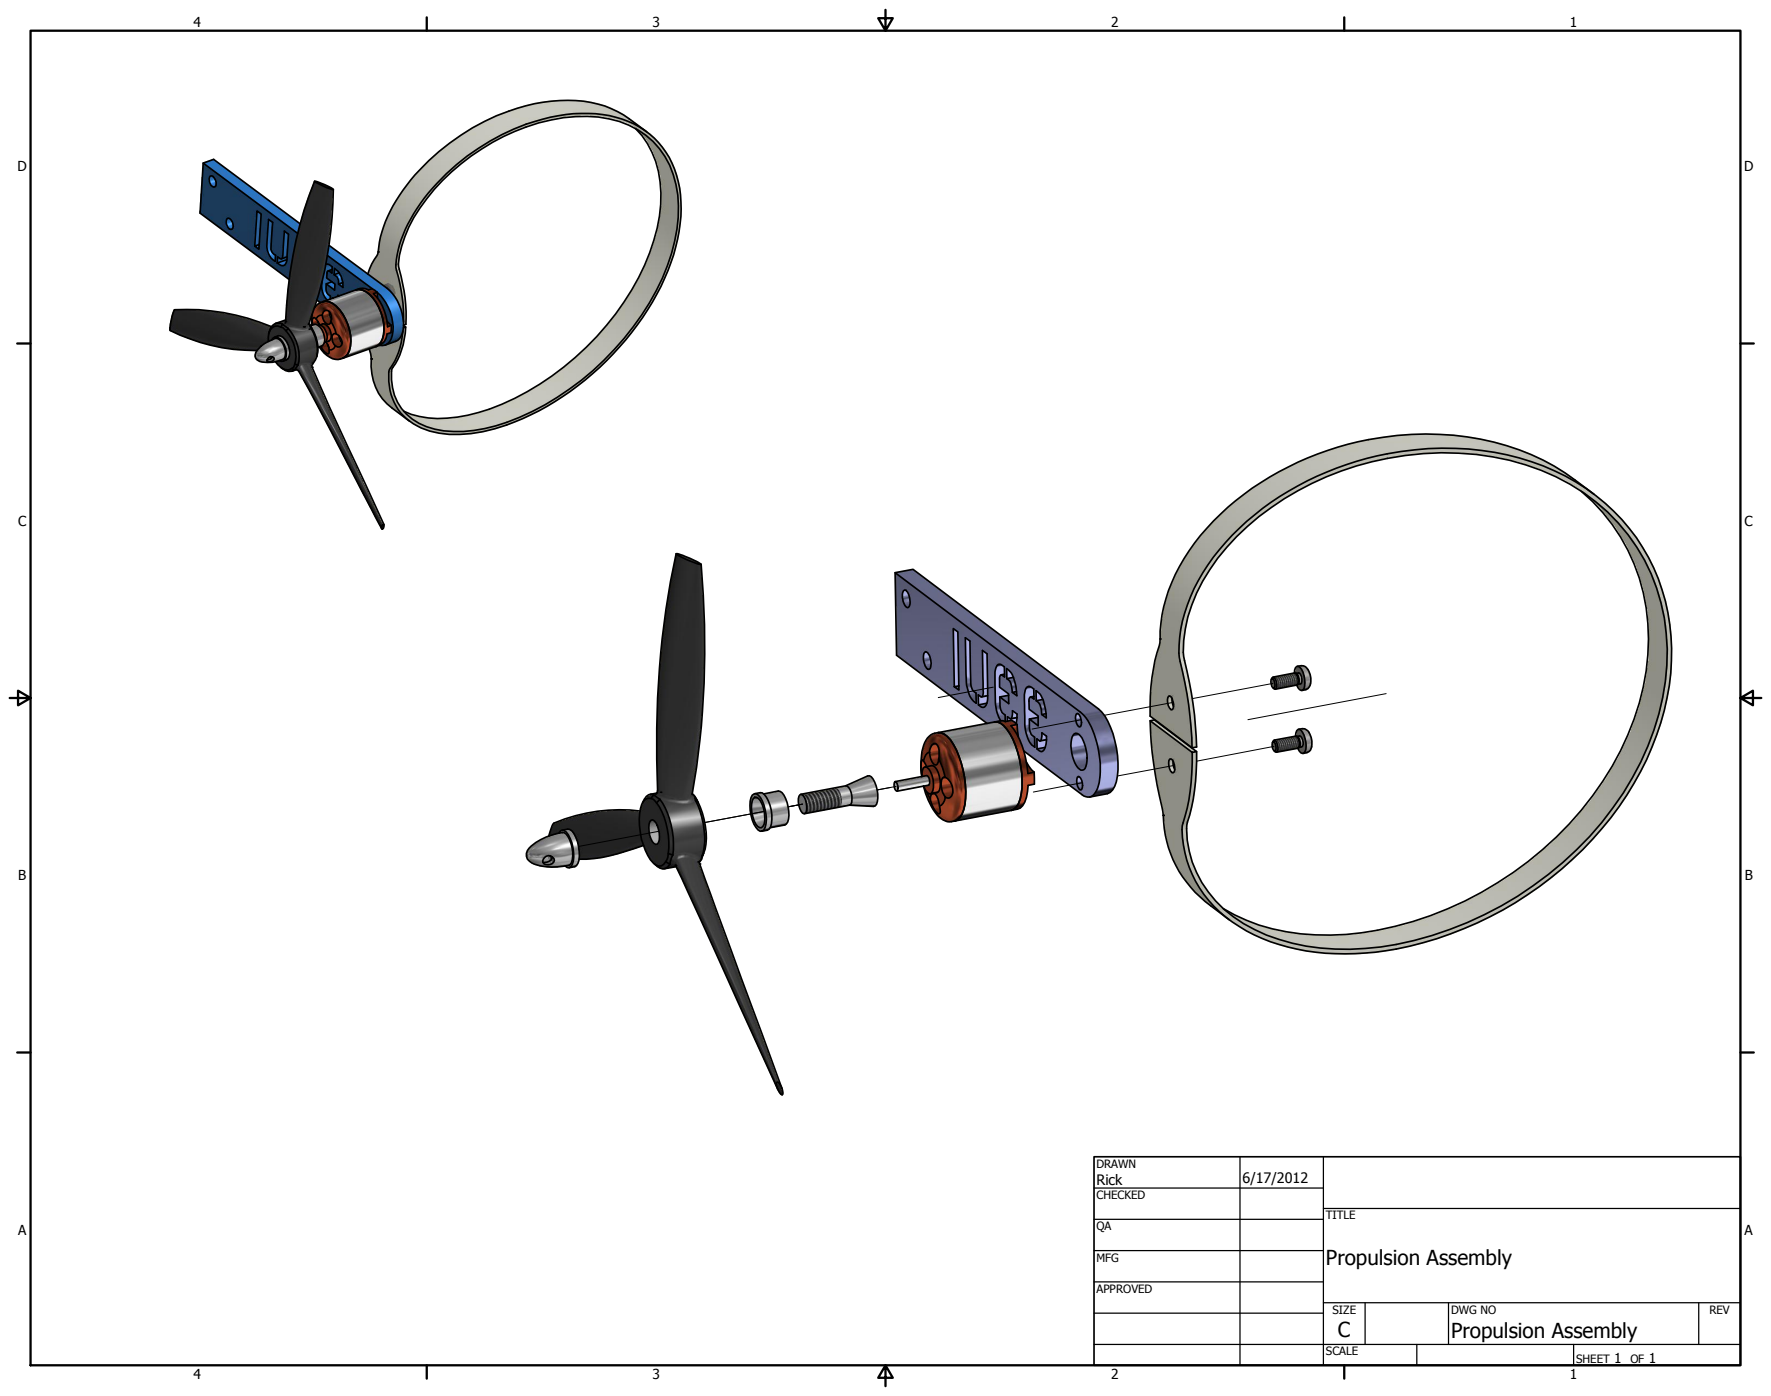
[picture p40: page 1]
SHEET 1 OF 1; DRAWN; CHECKED; MFG; APPROVED; Rick; DWG NO Propulsion Assembly; TITLE; Propulsion Assembly; SIZE C; SCALE; REV
